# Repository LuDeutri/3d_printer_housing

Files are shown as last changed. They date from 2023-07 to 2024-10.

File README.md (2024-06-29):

# 3d_printer_housing
This repo is to control diffrent functionalitys for an self-build housing of a 3d FDM printer based on klipper with an Raspberry Pi 4B and one STM32F103 bluepill board. An fire extinguisher system based on CO2 is included.

printer_view
printing_nozzle

## Setup:
- Anycubic Cobra Plus
- Raspberry Pi 4B
- STM32F103 (Bluepill)
- 3 Button (Fire_butn, Led_btn, PrinterSply_btn)
- WS2811 RGB Leds
- MQ-2 Gas sensor
- electric controlled magnetic pneumatic valve
- 450ml Sodastream (CO2)
- OSOYOO DSI display 5 zoll
- 12V Beeper
- 1x DSI pi camera, 1x usb pi camera
- 1x be quiet pwm fan
- multiple MOSFET switches

## Controller:
The main part is running on the stm32, the pi mainly controls the printer together with the printer hardware (HC32F460).
The stm32 and the pi are stacked and communcicate to each other about a simple GPIO bit communcication. With that the RGB leds and printer supply can be controlled in the webinterface.

  
 

**Bluepill:**
- RGB Leds (PWM with DMA data signal)
- MQ-2 gas sensor data read out
- Fire extinguisher (electronic controlled pneumatic valve)
- Buttons state
- Printer supply (2 MOSFET switches: L and N)
- Beeper (used for fire alarm)

**Pi:**
- Printer control (Klipper, webinterface Mainsail)
- Display (klipperScreen)
- DSI, USB camera (crowsnest)
- Cooling fan (controlled by pid regulator)

## Fire extinguisher:
The MQ-2 sensor is used to detect a fire inside the casing. The extinguisher is based on a sodastream CO2 gas bottle and a electronic controlled pneumatic valve to extinguish the fire.
Beside the sensor, an button at the side of the case can be used to activate the fire extiguisher or to deactivate the alarm sequence. An beeper and red fading leds are used to indicate the alarm.




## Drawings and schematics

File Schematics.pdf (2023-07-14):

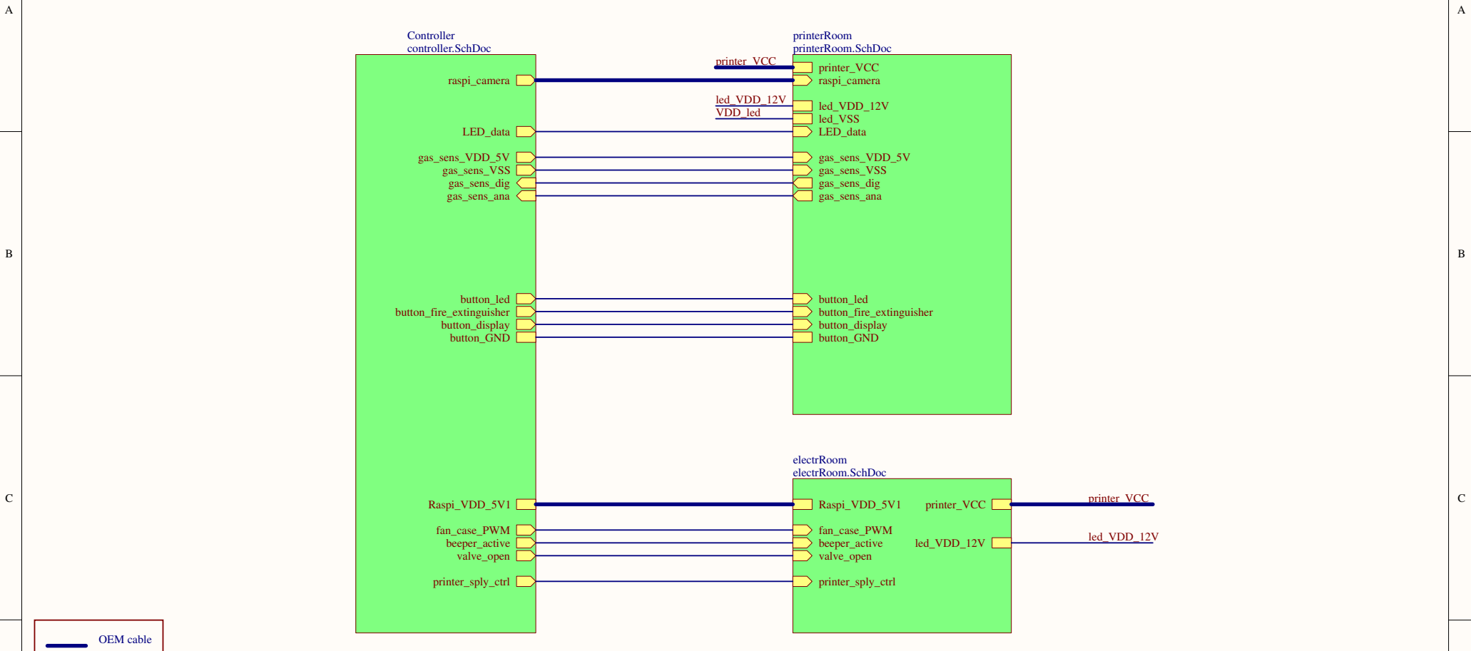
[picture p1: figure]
gas_sens_dig gas_sens_ana; button_display; button_led; LED_data; valve_open; beeper_active; button_fire_extinguisher; raspi_camera; gas_sens_VDD_5V gas_sens_VSS; Raspi_VDD_5V1; button_GND; printer_sply_ctrl; fan_case_PWM; Controller controller.SchDoc; printer_VCC; led_VDD_12V; electrRoom electrRoom.SchDoc; led_VSS; printerRoom printerRoom.SchDoc; led_VDD_12V VDD_led; OEM cable

D | D

## Raspberry Pi 3 A+

## Display

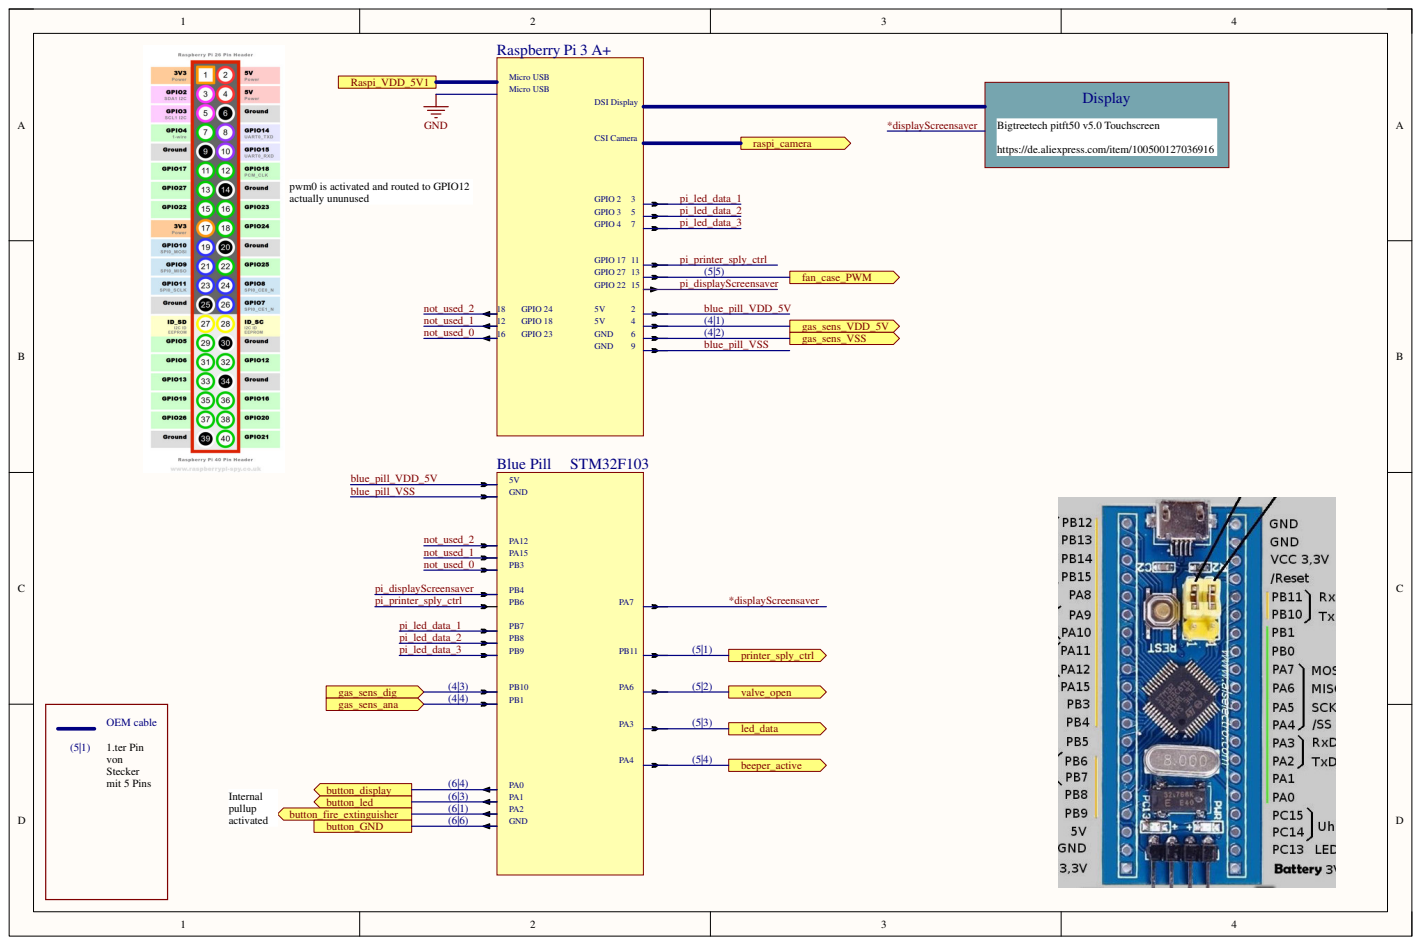
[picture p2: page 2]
Blue Pill; STM32F103; beeper_active; led_data; button_led button_fire_extinguisher; button_display; gas_sens_dig gas_sens_ana; pi_led_data_1 pi_led_data_2 pi_led_data_3; raspi_camera; GND; gas_sens_VDD_5V gas_sens_VSS; Raspi_VDD_5V1; valve_open; Internal pullup activated; GPIO 2 GPIO 3 GPIO 4; GPIO 17; 5V GND GND; DSI Display; CSI Camera; Micro USB Micro USB; *displayScreensaver; button_GND; printer_sply_ctrl; blue_pill_VDD_5V; pi_printer_sply_ctrl; blue_pill_VSS; fan_case_PWM GPIO 27 13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

https://de.aliexpress.com/item/100500127036916

pwm0 is activated and routed to GPIO12
actually ununused

## Fan

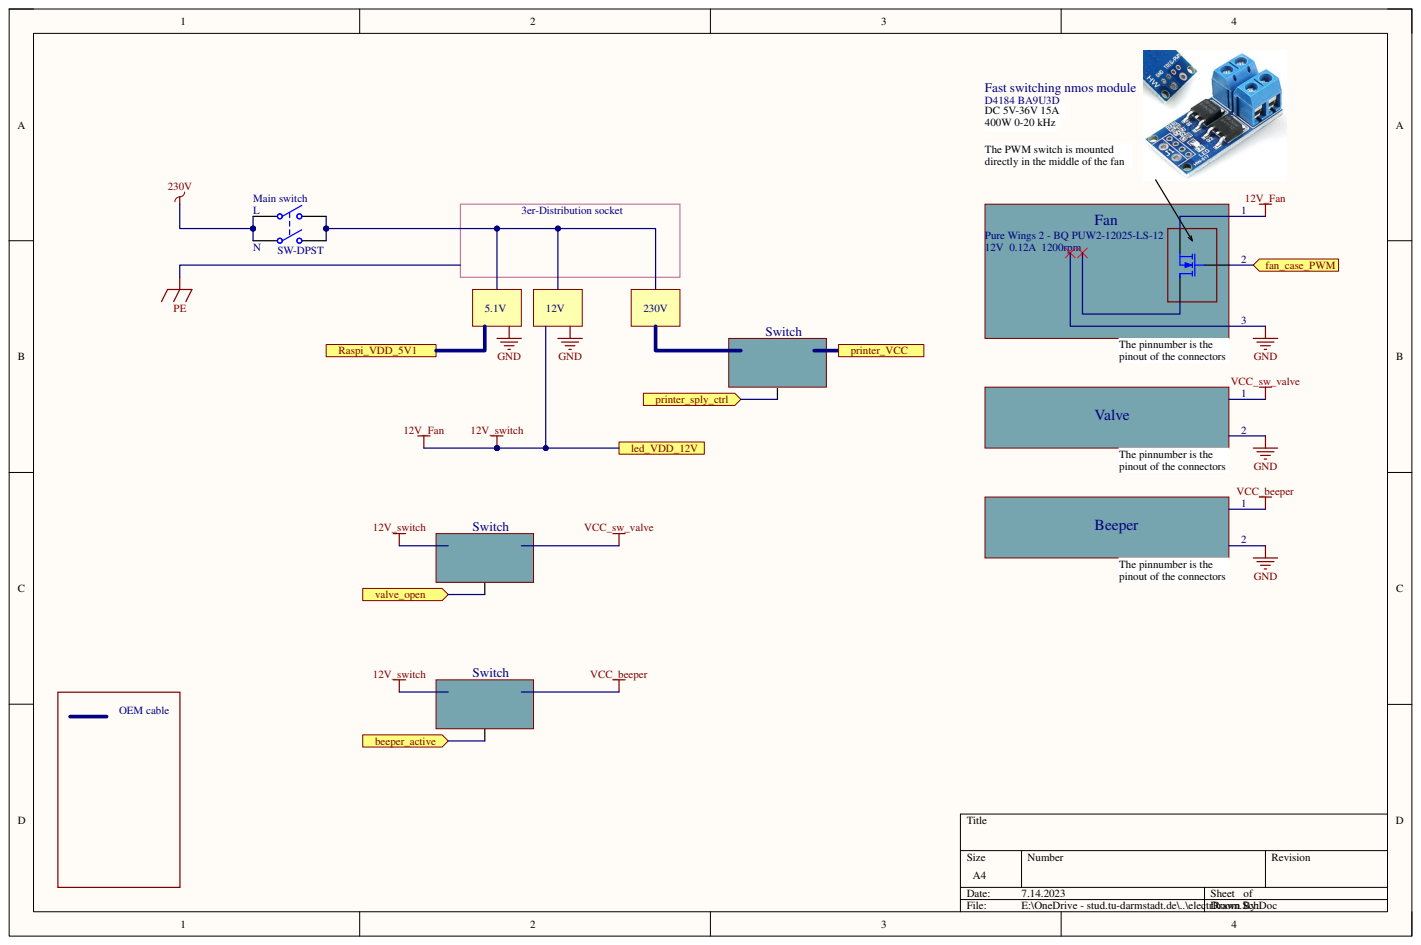
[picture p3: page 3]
Title; Number; RevisionSize; Date:; Sheet of; File:; E:\OneDrive - stud.tu-darmstadt.de\..\electrRoom.SchDocDrawn By:; Main switch; SW-DPST; 3er-Distribution socket; 12V_switch; Valve; Beeper; GND; 12V_Fan; VCC_sw_valve; valve_open; led_VDD_12V; VCC_beeper; Switch; fan_case_PWM; OEM cable; beeper_active; Raspi_VDD_5V1; printer_sply_ctrl; printer_VCC

Fast switching nmos module
400W 0-20 kHz

The PWM switch is mounted
directly in the middle of the fan

Pure Wings 2 - BQ PUW2-12025-LS-12
12V 0.12A 1200rpm

The pinnumber is the
pinout of the connectors

## 3D_printer

## Pi_Camera

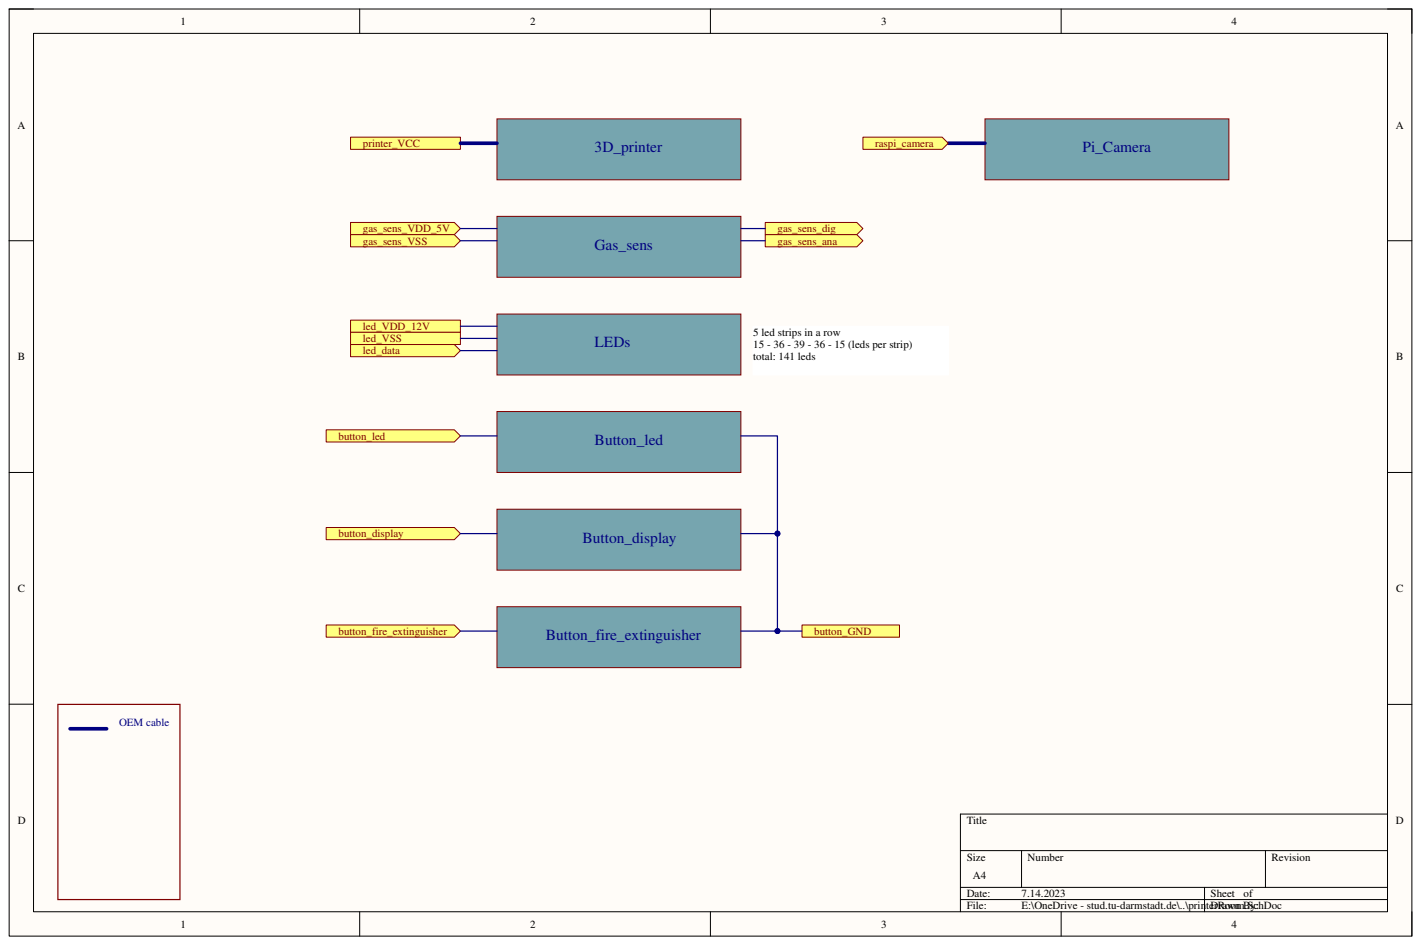
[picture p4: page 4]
Title; Number; RevisionSize; Date:; Sheet of; File:; E:\OneDrive - stud.tu-darmstadt.de\..\printerRoom.SchDocDrawn By:; LEDs; Button_led; Button_display; Button_fire_extinguisher; printer_VCC; led_VDD_12V; led_data; button_led; button_fire_extinguisher; button_display; Gas_sens; gas_sens_dig gas_sens_ana; led_VSS; OEM cable; button_GND; gas_sens_VDD_5V gas_sens_VSS; raspi_camera

5 led strips in a row
15 - 36 - 39 - 36 - 15 (leds per strip)
total: 141 leds

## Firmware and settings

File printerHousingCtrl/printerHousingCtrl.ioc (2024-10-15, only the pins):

Mcu.UserName=STM32F103C8Tx
PA0-WKUP.GPIO_Label=btn_PrinterSply
PA0-WKUP.Signal=GPIO_Input
PA1.GPIO_Label=btn_led
PA1.Signal=GPIO_Input
PA12.GPIO_Label=unused_0
PA12.Signal=GPIO_Output
PA13.Signal=SYS_JTMS-SWDIO
PA14.Signal=SYS_JTCK-SWCLK
PA15.GPIO_Label=unused_1
PA15.Signal=GPIO_Output
PA2.GPIO_Label=btn_fire_ExGuisher
PA2.Signal=GPIO_Input
PA3.Signal=S_TIM2_CH4
PA4.GPIO_Label=beeper
PA4.Signal=GPIO_Output
PA6.GPIO_Label=valve_open
PA6.Signal=GPIO_Output
PB1.GPIO_Label=gas_sens_analog
PB1.Signal=ADCx_IN9
PB10.GPIO_Label=gas_sens_digital
PB10.Signal=GPIO_Input
PB11.GPIO_Label=printer_sply_ctrl
PB11.Signal=GPIO_Output
PB3.GPIO_Label=unused_2
PB3.Signal=GPIO_Output
PB4.GPIO_Label=unused_4
PB4.Signal=GPIO_Input
PB6.GPIO_Label=pi_printer_sply_ctrl
PB6.Signal=GPIO_Input
PB7.GPIO_Label=pi_led_data_1
PB7.Signal=GPIO_Input
PB8.GPIO_Label=pi_led_data_2
PB8.Signal=GPIO_Input
PB9.GPIO_Label=pi_led_data_3
PB9.Signal=GPIO_Input
PC13-TAMPER-RTC.GPIO_Label=debug_led
PC13-TAMPER-RTC.Signal=GPIO_Output
PD0-OSC_IN.Signal=RCC_OSC_IN
PD1-OSC_OUT.Signal=RCC_OSC_OUT

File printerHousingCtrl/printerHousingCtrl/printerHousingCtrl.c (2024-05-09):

#include "printerHousingCtrl.h"

errDelay_t raspiLedInputOne;
errDelay_t raspiLedInputTwo;
errDelay_t raspiLedInputThree;
errDelay_t raspiPrinterSplyCtrl;
errDelay_t raspiScreenSaverCtrl;

bool tmpDataInOne;
bool tmpDataInTwo;
bool tmpDataInThree;

void printerHousingCtrl_init(){

	createErrDelay(&raspiLedInputOne, 1500);
	createErrDelay(&raspiLedInputTwo, 1500);
	createErrDelay(&raspiLedInputThree, 1500);
	createErrDelay(&raspiPrinterSplyCtrl, 1500);
	createErrDelay(&raspiScreenSaverCtrl, 1500);

	tmpDataInOne = false;
	tmpDataInTwo = false;
	tmpDataInThree = false;

	// Init modules
	button_init();
	fireExtinguisher_init();
	gasSensor_init();
	led_init();
	printer_init();
}

void printerHousingCtrl_main(){

	// Wait for finished init
	if (HAL_GetTick() < 1000)
		return;

	// Main loop
	while(true){
		// Update inputs
		button_update();
		updatePiInput();

		// Update submodules
		gasSensor_update();
		fireExtinguisher_update();
		led_update();
		printer_update();

		// Toggle debug led
		HAL_GPIO_WritePin(debug_led_GPIO_Port, debug_led_Pin, HAL_GetTick() % 1000 < 500);
	}
}

void updatePiInput(){
	if(HAL_GetTick() < 10000) // To ensure raspi has started completely
		return;

	// Check if the changed value is constant
	if(checkErrDelay(&raspiLedInputOne, tmpDataInOne != HAL_GPIO_ReadPin(pi_led_data_1_GPIO_Port, pi_led_data_1_Pin)))
		tmpDataInOne = HAL_GPIO_ReadPin(pi_led_data_1_GPIO_Port, pi_led_data_1_Pin);
	if(checkErrDelay(&raspiLedInputTwo, tmpDataInTwo != HAL_GPIO_ReadPin(pi_led_data_2_GPIO_Port, pi_led_data_2_Pin)))
		tmpDataInTwo = HAL_GPIO_ReadPin(pi_led_data_2_GPIO_Port, pi_led_data_2_Pin);
	if(checkErrDelay(&raspiLedInputThree, tmpDataInThree != HAL_GPIO_ReadPin(pi_led_data_3_GPIO_Port, pi_led_data_3_Pin)))
		tmpDataInThree = HAL_GPIO_ReadPin(pi_led_data_3_GPIO_Port, pi_led_data_3_Pin);

	// LED raspi pi inputs update
	leds.ledDataIn = (tmpDataInOne << 2) | (tmpDataInTwo << 1) | (tmpDataInThree);

	// Printer supply input update
	if(checkErrDelay(&raspiPrinterSplyCtrl, printer.splyCtrlRaspiInput != HAL_GPIO_ReadPin(pi_printer_sply_ctrl_GPIO_Port, pi_printer_sply_ctrl_Pin)))
		printer.splyCtrlRaspiInput = HAL_GPIO_ReadPin(pi_printer_sply_ctrl_GPIO_Port, pi_printer_sply_ctrl_Pin);
}

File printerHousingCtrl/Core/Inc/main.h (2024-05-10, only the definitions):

#define debug_led_Pin GPIO_PIN_13
#define debug_led_GPIO_Port GPIOC
#define btn_PrinterSply_Pin GPIO_PIN_0
#define btn_PrinterSply_GPIO_Port GPIOA
#define btn_led_Pin GPIO_PIN_1
#define btn_led_GPIO_Port GPIOA
#define btn_fire_ExGuisher_Pin GPIO_PIN_2
#define btn_fire_ExGuisher_GPIO_Port GPIOA
#define beeper_Pin GPIO_PIN_4
#define beeper_GPIO_Port GPIOA
#define valve_open_Pin GPIO_PIN_6
#define valve_open_GPIO_Port GPIOA
#define gas_sens_analog_Pin GPIO_PIN_1
#define gas_sens_analog_GPIO_Port GPIOB
#define gas_sens_digital_Pin GPIO_PIN_10
#define gas_sens_digital_GPIO_Port GPIOB
#define printer_sply_ctrl_Pin GPIO_PIN_11
#define printer_sply_ctrl_GPIO_Port GPIOB
#define unused_0_Pin GPIO_PIN_12
#define unused_0_GPIO_Port GPIOA
#define unused_1_Pin GPIO_PIN_15
#define unused_1_GPIO_Port GPIOA
#define unused_2_Pin GPIO_PIN_3
#define unused_2_GPIO_Port GPIOB
#define unused_4_Pin GPIO_PIN_4
#define unused_4_GPIO_Port GPIOB
#define pi_printer_sply_ctrl_Pin GPIO_PIN_6
#define pi_printer_sply_ctrl_GPIO_Port GPIOB
#define pi_led_data_1_Pin GPIO_PIN_7
#define pi_led_data_1_GPIO_Port GPIOB
#define pi_led_data_2_Pin GPIO_PIN_8
#define pi_led_data_2_GPIO_Port GPIOB
#define pi_led_data_3_Pin GPIO_PIN_9
#define pi_led_data_3_GPIO_Port GPIOB

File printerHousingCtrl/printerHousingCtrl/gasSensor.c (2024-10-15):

#include "gasSensor.h"

gasSensor_t gasSensor;

void gasSensor_init(){
	gasSensor.fireDetected = false;
	gasSensor.fireDetectedTime = 0;
	gasSensor.gasSensAnalog = 0;
	gasSensor.gasSensDig = 0;
}

void gasSensor_update(){
	// Update data
	gasSensorReadData();

	// Handle data
	if ((gasSensor.gasSensDig && !ENABLE_ANALOG_GAS_VALUE) 			// Fire detected by the sensor
			|| (gasSensor.gasSensAnalog > THRESHOLD_GAS_SENSOR_FIRE_DETECTED && ENABLE_ANALOG_GAS_VALUE)) {
		if(gasSensor.fireDetectedTime == 0) // Safe time fire is detected
			gasSensor.fireDetectedTime = HAL_GetTick();
		else if(gasSensor.fireDetectedTime + ERR_DELAY_FIRE_DETECTED < HAL_GetTick()){ // Wait err_delay
			gasSensor.fireDetected = true;
			if(gasSensor.gasSensAnalog > THRESHOLD_GAS_SENSOR_FIRE_DETECTED_ALARM && ENABLE_ANALOG_GAS_VALUE)
				fireExtinguisherActivate();				// Activate the fire extinguisher immediately
			else
				fireExtinguisherStartCount();			// Activate the fire extinguisher sequence
		}
	} else
		gasSensor.fireDetectedTime = 0;
}

/* only for calibration used
uint16_t arr[1000];
uint16_t ii = 0;
uint32_t timee = 0;
*/
void gasSensorReadData(){
	if(HAL_GetTick() < GAS_SENSOR_CALIBRATION_TIME) // Wait x seconds to calibrate the sensor first
		return;

	gasSensor.gasSensDig = HAL_GPIO_ReadPin(gas_sens_digital_GPIO_Port, gas_sens_digital_Pin);

	if (ENABLE_ANALOG_GAS_VALUE){
		HAL_ADC_Start(GAS_SENSOR_ADC);
		HAL_ADC_PollForConversion(GAS_SENSOR_ADC, HAL_MAX_DELAY);
		gasSensor.gasSensAnalog = HAL_ADC_GetValue(GAS_SENSOR_ADC);

		/* only for calibration used
		if(HAL_GetTick() < timee + 500) return;

		if(ii == 1000) ii =0;
		arr[ii] = gasSensor.gasSensAnalog;
		ii++;
		timee = HAL_GetTick();
		*/
	}
}

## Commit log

2023-07-11 add schematics
    [3d_printer_housing.PrjPcb, 3d_printer_housing.SchDoc, controller.SchDoc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]
2023-07-12 printerSplyCtrl in eigene header und source files umgelagert und fertig definiert pi steuerungssignal für den screensaver hinzugefügt als input des stm32 displayScreensaver in eigene header und sourc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
2023-07-12 schematics updated, LED output pin changed (must be an timer pin) new pin for screensaver activation through rasberry pi added
    [controller.SchDoc]
2023-11-17 stm32xcubeide update
2024-04-01 schmematics folder deleted
    [3d_printer_housing.PrjPcb, 3d_printer_housing.SchDoc, controller.SchDoc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]
2024-04-01 schematics pdf file added
2024-04-01 datasheet WS2811 leds added
2024-04-01 raspi config added
    [3d_printer_klipper_raspi_config.txt]
2024-04-03 timer channel changed TIM1 CH1 --> TIM2 CH4
2024-04-22 fire alarm must not be activated after deactivating trough the fire button without an reset
    [fireExtinguisher.c]
2024-04-22 inputs of raspi for printer supply will not be accepted until 10.000 seconds after start
2024-05-09 led test states deleted, rainbow state changed to color wheel fade state
2024-05-09 runningLight start animation values added, reset brightness in nextState method added, fire detection led state changed, fire button led state changed, setAllLeds changed into setSPecificLeds for all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
2024-05-09 not used button display deleted
2024-05-09 errDelay include added, timer time for light in electronics room added, some parameters changed, display screensaver defines deleted, gasSensor boolean changed into define
2024-05-09 fire button diffrent states added: first push = activate alarm, second push = mute alarm, third push = deactivate fire sequence (its not possible to activate the fire sequence again), fourth push = r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
    [fireExtinguisher.c]
2024-05-09 fire button states added, valve ctrl changed, documentation continued
2024-05-09 analog gas sensor value implemented, errDelay included
2024-05-09 errDelays for all pi inputs added top prevent bad connections errors, display screensaver input deleted
    [printerHousingCtrl.c]
2024-05-10 button to enable the printer sply added
2024-05-10 unused deleted, pin screensaver in unused_4 renamed
2024-05-13 gas sensor analog value disabled
2024-05-13 initial state 3d printer changed to off
2024-10-15 bug fixes, calibration (heat up) time changed for gas sensor, analog value is used now
    [gasSensor.c]
2024-10-15 gas sensor trigger time changed, new defines for gas sensor added
2024-10-15 internal pullup resistor for digital input gas sensor activated (if the sensor has no connection, it will cause in a fire alarm now)
2024-11-17 thresholds for gas sensor adjusted

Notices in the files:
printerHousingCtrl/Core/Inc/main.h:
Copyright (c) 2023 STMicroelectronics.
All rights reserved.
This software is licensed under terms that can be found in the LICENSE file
